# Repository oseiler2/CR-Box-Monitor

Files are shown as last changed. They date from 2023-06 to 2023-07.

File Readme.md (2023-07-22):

# Fan controller and CO2 Monitor for Corsi-Rosenthal boxes

An ESP32 based controller with integrated CO2 Monitor for PC-fans used in [Corsi-Rosenthal boxes](https://en.wikipedia.org/wiki/Corsi%E2%80%93Rosenthal_Box) and other diy air filters.

See [here](https://github.com/oseiler2/CO2Monitor) for some additional background on CO2 monitoring.

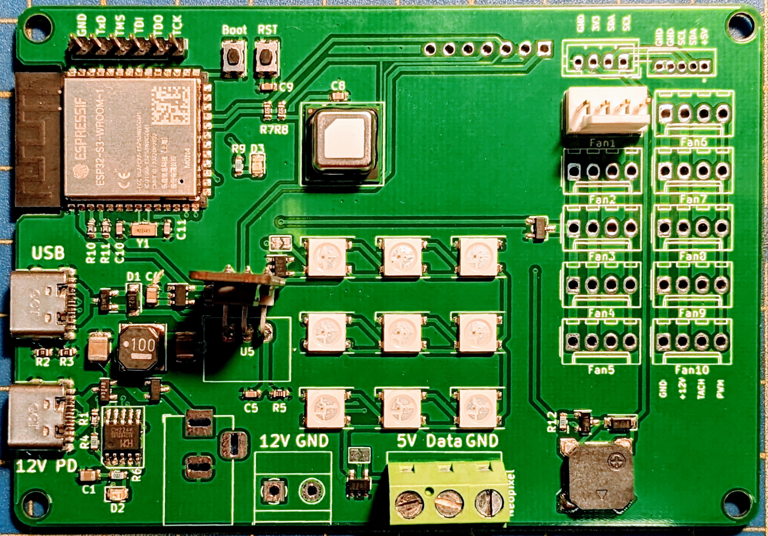
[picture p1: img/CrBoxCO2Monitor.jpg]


## Motivation

Many commercial air filters are expensive, under-dimensioned and noisy. Corsi-Rosenthal boxes are easy to make and very efficient air filters used to clean the air from airborne viral particles, allergens, smoke and other irritants.

The classic CR box design uses a box fan, which has some disadvantages:
- hard to get in some regions
- using mains voltage which can be a perceived or very real risk in some environments, e.g. classrooms
- can be noisy (depending on the fan)
- not easy to control

More recent designs have been replacing the box fan with an array of comparatively large, pressure optimised PC case fans, for example 9 x 140mm fans in a 3x3 grid on top of a 20 inch filter panel CR box. The smaller size of the fans also allows more flexibility in designing more portable CR boxes using 2 smaller filter panels.

Low speed PC fans are also much quieter and operate on safe 12V power.

By keeping the noise as low as possible and addressing the other above concerns the acceptance and tolerance of CR Boxes is increased. Commercial air cleaners are often turned off, or set to minimum levels, which contradicts their purpose. Further this controller and the operation of the fans and effectiveness can be monitored remotely.

[Learn more about this small CR box pictured below](https://github.com/oseiler2/HalfSizeCrBox)

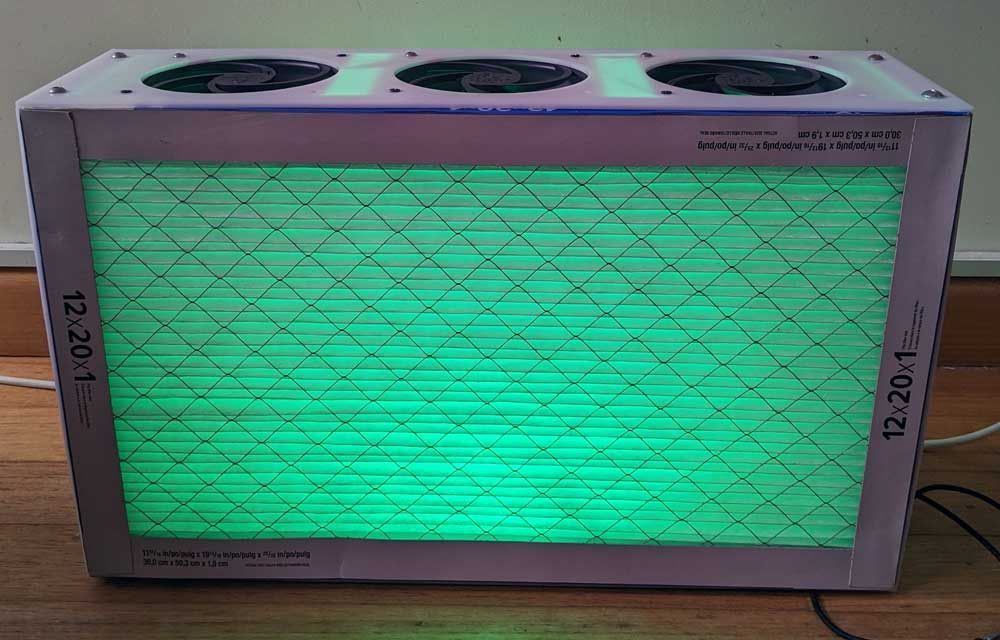
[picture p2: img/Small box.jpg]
Small CR box (https://github.com/oseiler2/HalfSizeCrBox)


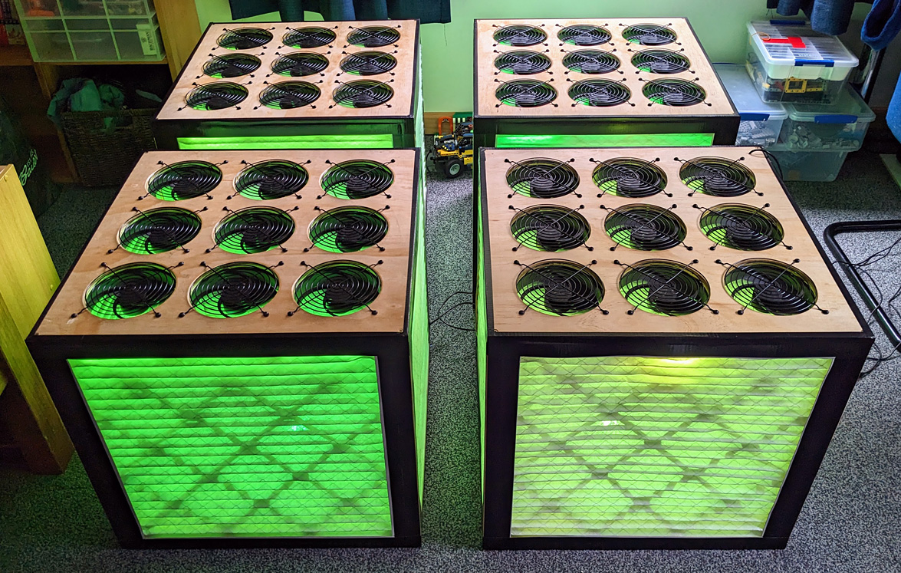
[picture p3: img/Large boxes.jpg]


# Sections

- [Features](#features) gives an overview of the capabilities and general operation
- [Hardware](#hardware) describes the board in more detail, which fans to use and how to connect them
- [PCBs](#pcbs) has more details on the design of the boards
- [Firmware](#firmware) describing the device's software features and how to use them
- [Cofiguration](#configuration) describing the device's software features and how to use them
- [Sensors](#sensors) has more information on the available sensors
- [Calibration](#calibration) has some important information on keeping the readings accurate

# Features

## General operation

The controller constantly assesses the air quality using the integrated CO2 monitor, air quality data via MQTT, or additional sensors connected via I2C, and regulates the fan speed accordingly. This will keep the airflow and related noise low while the air quality is generally good, either from good natural ventilation, or vacancy of the room. The integrated lights can reflect the air quality by showing a continuous spectrum from green via yellow to red and purple, or if configured just cycle through all colours. An integrated buzzer can also be used to alter on air quality threshold changes.

MQTT integration allows capturing all measured data and displaying on dashboards, as [documented here](https://github.com/oseiler2/CO2Monitor/blob/main/docker/docker.md).

## Key features

- Speed controller for 10 or more PC fans to regulate air flow depending on air quality
- compatible with 3 (no pwm) or 4 (pwm) pin. Non-pwm 3 pin fans are controlled using an integrated MosFET driven by a PWM signal
- 9 bright internal colour LEDs to indicate air quality with the option to connect more WS2812 (Neopixel) based LEDs
- integrated CO2, temperature and humidity sensor,
- alternatively capability to consume CO2 readings from another CO2 monitor via MQTT (eg [CO2Monitor](https://github.com/oseiler2/CO2Monitor))
- WiFi and MQTT enabled for reporting and/or consuming CO2 readings and remote configuration
- integrated buzzer to alert of poor air quality, or changes in air quality
- USB-PD compatibility to power everything off a USB-PD enabled power supply (phone charger)
- 12V direct input using 5.5x2.1mm Barrel Jack
- I2C connector to integrate other sensors
- SPS30 Particulate Matter sensor connector

# Firmware




## Firmware flashing

The firmware can be flashed onto the board directly from a supported browser [from here](https://oseiler2.github.io/CR-Box-Monitor/).

## Wifi

When not connected to a configured WiFi, the controller will automatically create an Access Point using the SSID CR-Box-<ESP32mac>. Connecting to this AP allows the Wifi credentials for the monitor to be set. The AP can also be forced by pressing the `Boot` button for less than 2 seconds.

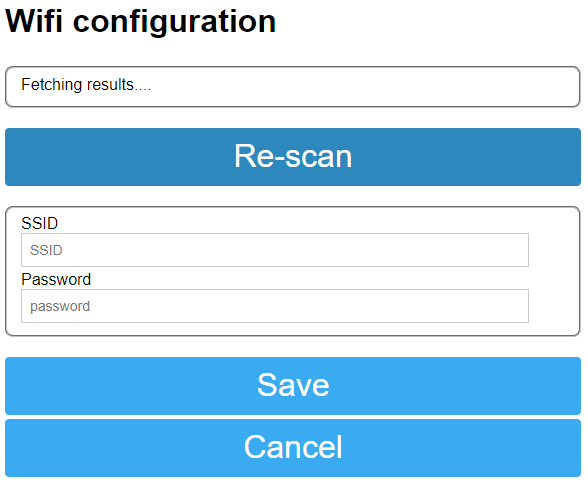
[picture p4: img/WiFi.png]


The firmware also supports WiFi configuration using [Improv Wifi](https://www.improv-wifi.com/) when connected via USB to a computer and using a supported browser [from here](https://oseiler2.github.io/CR-Box-Monitor/).

A password for the AP can be configured in the file `extra.ini` which needs to be created by copying [extra.template.ini](extra.template.ini) and applying the desired changes.

## Configuration

The controller is configured via the `config.json file on the ESP32 file system. There are 3 ways the configuration can be changed:

- via the Web Interface
- by directly editing [config.json](data/config.json) and uploading it via `Upload Filesystem Image`
- via MQTT (once connected)

### Web Interface

Navigating a browser to the controller's IP address will open the Web Interface. Here you can select to Change the Wifi configuration, the more generic device configuration, look at logs or reboot the device.

The Web Interface can be protected by setting a username and password in the file `extra.ini` which needs to be created by copying [extra.template.ini](extra.template.ini) and applying the desired changes.

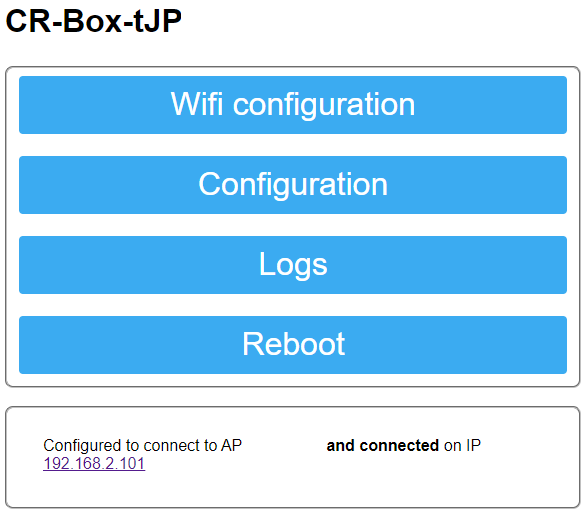
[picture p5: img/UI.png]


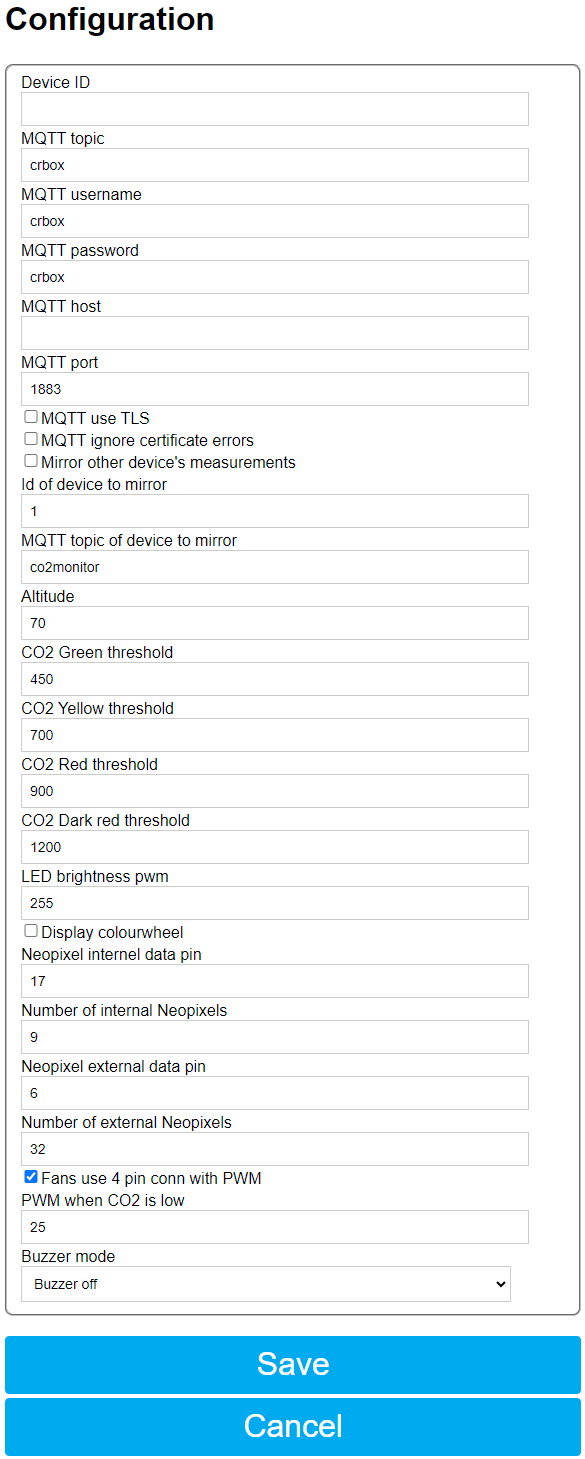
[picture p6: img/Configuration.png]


- `Device ID` unique id of the device, mainly used for MQTT
- `MQTT topic`, `MQTT username` , `MQTT password`, `MQTT host`, `MQTT port`, `MQTT TLS`, `MQTT ignore certificate errors` are all used to configure the MQTT host connection
- `Mirror other device's measurements` can be enabled to consume readings from another monitor using the `ID of device to mirror` and `MQTT topic of device to mirror` MQTT settings if the controller is not outfitted with a CO2 sensor
- `Altitude` is used to calibrate the SCD30/SCD4x CO2 sensor
- `CO2 Green threshold` sets the lower limit at which the fans will be set to idle speed. Any higher CO2 measurements increase the fan speed.
- `CO2 Yellow threshold`, `CO2 Red threshold`, `CO2 Dark threshold` set the limits for changing the LED colours and fan speed. The fan speed is continously increasing from the idle speed (green) to 50% (yellow) to full speed (red).
- `LED brightness PWM` sets the LED brightness on a scale from 0 to 255
- `Display colourwheel` changes the LEDs to circle throw all colours instead of reflecting air quality readings. This can be useful when no attention should be drawn to current CO2 levels.
- `Neopixel internal data pin` should be left at `17` and `Number of internal Neopixels` at `9` unless a different PCB configuration is being used.
- `Neopixel external data pin` should be set to `0` when no additional Neopixels are connected to the screw terminal, and set to `6` otherwise. `Number of external Neopixels` should be set to the number of additional Neopixels
- `Fans use 4 pin connector with PWM` needs to be enabled to control PWM enabled fans. If unticked the fan GND connection will be PWM driven to control 3-pin fans.
- `PWM when CO2 is low` sets the idle fan speed on a scale from 0 to 255. This should be set high enough that the fans do start up and keep spinning slowly, otherwise sufficient airflow cannot be guaranteed and the internal CO2 sensor might not give accurate readings.
- `Buzzer mode` configures the integrated buzzer to be always off, beep on every level change, or give a number of beeps depending on the CO2 level for each measurement.

### MQTT

Sensor readings can be published via MQTT for centralised storage and visualition. Each node is configured with its own id and will then publish under `crbox/<id>/up/sensors`. The top level topic `crbox` is configurable. Downlink messages to nodes can be sent to each individual node using the id in the topic `crbox/<id>/down/<command>`, or to all nodes when omitting the id part `crbox/down/<command>`

SCD3x/SCD4x

```
{
  "co2": 752,
  "temperature": "21.6",
  "humidity": "52.1",
  "fanPwm": 25
}
```

BME680

```
{
  "iaq": 19,
  "temperature": "19.2",
  "humidity": "75.6",
  "pressure": 1014
}
```

SPS30

```
{
  "pm0.5": 16,
  "pm1": 19,
  "pm2.5": 19,
  "pm4": 19,
  "pm10": 19
}
```

Sending `crbox/<id>/down/getConfig` will triger the node to reply with its current settings under `crbox/<id>/up/config`

```
{
  "appVersion": "1.0",
  "mac": "xxyyzz",
  "ip": "1.2.3.4",
  "scd40": true,
  "scd30": true,
  "bme680": true,
  "sps30": true,
  "sps30AutoCleanInt": 604800,
  "sps30Status": 0,
  "mqttTopic": "crbox",
  "mqttUsername": "crbox",
  "mqttHost": "1.2.3.4",
  "mqttServerPort": 1883,
  "mqttUseTls": true,
  "mqttInsecure": false,
  "mqttMirror": false,
  "mqttMirrordeviceId": 1,
  "mqttMirrorTopic": "co2monitor",
  "altitude": 5,
  "co2GreenThreshold": 450,
  "co2YellowThreshold": 700,
  "co2RedThreshold": 900,
  "co2DarkRedThreshold": 1200,
  "brightness": 255,
  "colourWheel": false,
  "neopixelIntData": 17,
  "neopixelIntNumber": 9,
  "neopixelExtData": 6,
  "neopixelExtNumber": 32,
  "fanHasPwm": true,
  "minPwm": 25,
  "buzzerMode": 0,
  "tempOffset": "4.0"
}
```

A message to `crbox/<id>/down/setConfig` will set the node's configuration to the provided parameters. Note that changes to the hardware configuration will trigger a reboot.

```
{
  "deviceId": 1,
  "mqttUsername": "crbox",
  "mqttPassword": "crbox",
  "mqttTopic": "crbox",
  "mqttUsername": "crbox",
  "mqttHost": "1.2.3.4",
  "mqttServerPort": 1883,
  "mqttUseTls": true,
  "mqttInsecure": false,
  "mqttMirror": false,
  "mqttMirrordeviceId": 1,
  "mqttMirrorTopic": "co2monitor",
  "altitude": 5,
  "co2GreenThreshold": 450,
  "co2YellowThreshold": 700,
  "co2RedThreshold": 900,
  "co2DarkRedThreshold": 1200,
  "brightness": 255,
  "colourWheel": false,
  "neopixelIntData": 17,
  "neopixelIntNumber": 9,
  "neopixelExtData": 6,
  "neopixelExtNumber": 32,
  "fanHasPwm": true,
  "minPwm": 25,
  "buzzerMode": 0,
  "tempOffset": "4.0"
}
```

A message to `crbox/<id>/down/setTemperatureOffset` will set the SCD3x/SCD4x's temperature offset (float, °C):

```
4.0
```

A message to `crbox/<id>/down/calibrate` will manually calibrate the SCD3x/SCD4x sensor to the given value:

```
412
```

A message to `crbox/<id>/down/setSPS30AutoCleanInterval` will set the SPS30 fan auto-clean interval in seconds to the given value:

```
604800
```

A message to `crbox/<id>/down/cleanSPS30` will run a fan clean on the SPS30.

A message to `crbox/<id>/down/installMqttRootCa` will attempt to install the pem-based ca cert in the payload as root cert for tls enabled MQTT connections. A connection attempt will be made using the configured MQTT settings and the new cert, and if successful the cert will be persisted, otherwise discarded.

A message to `crbox/<id>/down/installRootCa` will install the pem-based ca cert in the payload as root cert for OTA update requests.

A message to `crbox/<id>/down/ota` will trigger the OTA polling mechnism if configured.

A message to `crbox/<id>/down/forceota` will force an OTA update using the URL provided in the payload.

A message to `crbox/<id>/down/reboot` will trigger a reset on the node.

A message to `crbox/<id>/down/resetWifi` will wipe configured WiFi settings (SSID/password) and force a reboot.

### MQTT TLS support

To connect to an MQTT server using TLS (recommended) you need to enable TLS in the configuration by setting `mqttUseTls` to `true`. You also need to supply a root CA certificate in PEM format on the file system as `/mqtt_root_ca.pem` and/or a client certificate and key for using mTLS as `mqtt_client_cert.pem` and `mqtt_client_key.pem`. These files can be uploaded using the `Upload Filesystem Image` project task in PlatformIO. Alternatively you can set `mqttInsecure` to `true` to disable certificate validation altogether.

# Hardware

## Power

The board can be powered in 3 different ways:

1. Using a USB-PD capable power supply or phone charger, capable of delivering 12V and enough power (25W+). [charger - amazon.au](https://www.amazon.com.au/dp/B09NDG1MPP)
2. 12V direct input using 5.5x2.1mm Barrel Jack receptable
3. 12V screw terminal

Make sure to use a power supply that can deliver enough power. 140mm fans need about 150mA each. Each Neopixel can draw up to 60mA (540mA for all 9 integrated ones). The 5V DC-DC regulator is dimensioned for up to 2A - take that in mind when connecting additional Neopixels.

## Fans

Make sure to use pressure optimised low speed fans that are capable of delivering airflow at sufficient static pressure e.g. [Arctic P14](https://www.arctic.de/en/P14/ACFAN00136A) (2.4 mm H2O, 0.3 Sone, 123 m³/h) or [Arctic P12](https://www.arctic.de/en/P12/ACFAN00135A) (2.2 mm H20, 0.3 Sone, 95.7 m³/h).

The controller can read the RPM signal from the fan connected to the `Fan 1` connector

## Fan hub

The main board features up to 10 connectors for 3 or 4 pin fans. For builds where the fan cables are too short to reach to the main PCB, or when more than 10 fans should be connected, the fan hub PCB can be used to connect another 9 fans via an extension cable. To enale reading the RPM sigal connect the fan hub extension cable to the `Fan 1` connector on the main board and to the `Up` connector on the fan hub.

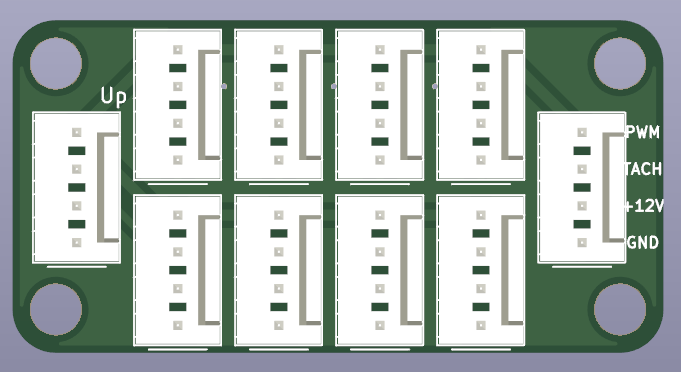
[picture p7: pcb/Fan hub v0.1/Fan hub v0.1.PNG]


## Additional Neopixels

Additional [Neopixel strips](https://www.adafruit.com/category/183) can be connected using the dedicated screw terminal. Make sure to not overload the power supply and integrated 5V 2A linear regulator.

# PCBs

Main board [sources](pcb/CrBoxCo2Monitor%20V0.1/), [gerber files](pcb/CrBoxCo2Monitor%20V0.1/CrBoxCo2Monitor%20V0.1.zip) and [parts list](pcb/CrBoxCo2Monitor%20V0.1/bom.md).

Fan hub [sources](pcb/Fan%20hub%20v0.1/) and [gerber files](pcb/Fan%20hub%20v0.1/Fan%20hub%20v0.1.zip).

3d printable [board holder](stl/PCB%20holder.STL) using M3 threaded inserts

# Sensors

The presence of supported I2C based sensors/displays will be automatically detected on start-up.

## SCD3x

A SCD3x NDIR CO2 sensor can be connected to the designated footprint and will provide CO2, temperature and humidity readings via I2C. It supports a separate ready signal which is connected to the ESP32.

## SCD4x

A SCD4x NDIR CO2 sensor can be soldered directly onto the pcb and provides CO2, temperature and humidity readings via I2C.

## BME680

A BME680 sensor can be connected via the I2C JST header [Adafruit BME680](https://www.adafruit.com/product/3660), [STEMMA to JST SH Cable](https://www.adafruit.com/product/4424) to provide additional VOC and AIQ measurements.

## SPS30 Particulate matter sensor

The SPS30 sensor can be connected to the dedicated connector using a JST-ZR cable.

## other

Other I2C based sensors can be wired using the JST-PH I2C header.

# Calibration

CO2 sensors need to be regularly calibrated to provide reliable measurements. The used sensors support auto-calibration and that is enabled in the firmware. It works by looking over measurements over a period and calibrating the lowest value against 420ppm (configurable in the firmware). This is based on the assumption that the monitor 'sees' clean outside air about once a week. If that cannot be achieved the firmware also allows for a forced calibration against a given value. Please also make sure to set the altitude setting according to the monitor location. For details please check the sensor's datasheets.

Manual calibration can be triggered by pressing the `Boot` button for more than 5 seconds. Make sure the monitor has been exposed to fresh outside air for a while and be careful not to breathe towards the monitor when doing this.

Calibration can also be triggered remotely via [MQTT](#mqtt).

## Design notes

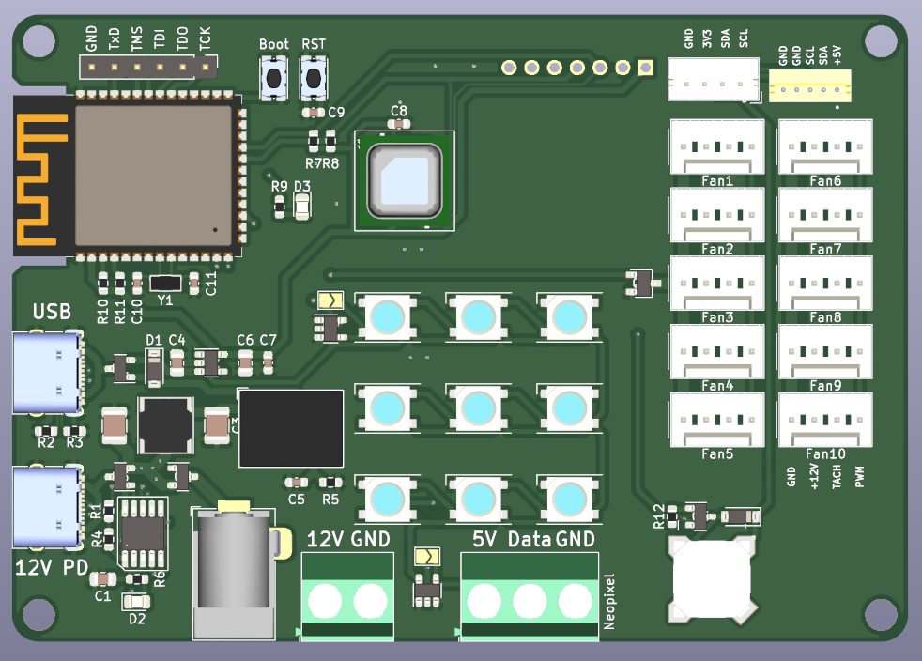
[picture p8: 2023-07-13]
pcb/CrBoxCo2Monitor V0.1/CR CO2 Monitor v0.1.png

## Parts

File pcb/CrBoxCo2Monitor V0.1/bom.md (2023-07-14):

# BOM

Note: the components marked in the 'Function' column are optional and only needed for the mentioned function.
For example if you want the second USB port to power the PCB with 12V via a USB-C PD power supply you need to populate all components marked with USB-PD.

| Quantity | Designator | Description | Function (optional) | Footprint | Part # | Supplier | Alternative |
| --- | --- | --- | --- | --- | --- | --- | --- |
| 1 | BZ1 | Buzzer | Buzzer | | ST-03BHT | [DigiKey](https://www.digikey.com/en/products/detail/soberton-inc/ST-03BHT/16354830) | |
| 1 | C1 | 10μF | USB-PD | 0805 | | | |
| 2 | C4, C6 | 10μF | | 0805 | | | |
| 1 | C2 | 10μF/50V MLCC | | 1210 | CL32B106KBJNNNE | [DigiKey](https://www.digikey.co.nz/en/products/detail/samsung-electro-mechanics/CL32B106KBJNNNE/3889045) | |
| 1 | C3 | 4.7μF/50V MLCC | | 1210 | CL32B475KBUYNNE | [DigiKey](https://www.digikey.co.nz/en/products/detail/samsung-electro-mechanics/CL32B475KBUYNNE/3886950) | |
| 4 | C5, C7, C8, C9 | 100nF | | 0603 | | | |
| 1 | D1 | Schottky diode 20V 500MA | | SOD-123 | MBR0520 | [DigiKey](https://www.digikey.co.nz/en/products/detail/micro-commercial-co/MBR0520-TP/717250) | |
| 1 | D2 | LED yellow 2mA 2.1V | USB-PD | 0805 | KPT-2012YC | [Element14](https://nz.element14.com/kingbright/kpt-2012yc/led-0805-yellow-8mcd-588nm/dp/2099243) | |
| 1 | D3 | LED green 2mA 2.65V | | 0805 | KPT-2012LVZGCK | [Element14](https://nz.element14.com/kingbright/kpt-2012lvzgck/led-green-50mcd-525nm-smd/dp/2610419) | |
| 1 | D4 | 200mA general purpose diode | Buzzer | SOD-123 | MMSD4148 | [DigiKey](https://www.digikey.co.nz/en/products/detail/onsemi/MMSD4148/1048639) | |
| 9 | D10, D11, D12, D13, D14, D15, D16, D17, D18 | WS2812B | | 5050 | | [AliExpress](https://www.aliexpress.com/item/1005002653014067.html) | |
| 1-10 | Fan1, Fan2, Fan3, Fan4, Fan5, Fan6, Fan7, Fan8, Fan9, Fan10 | 3/4 pin Molex_KK-254 | | | | [AliExpress](https://www.aliexpress.com/item/32961935772.html) | [DigiKey](https://www.digikey.com/en/products/detail/sullins-connector-solutions/SWR25X-NRTC-S04-ST-BA/2769654) |
| 1 | J1 | USB4105-GF-A-120 | | | | [DigiKey](https://www.digikey.com/en/products/detail/gct/USB4105-GF-A-120/14559037) | |
| 1 | J2 | USB4105-GF-A-120 | USB-PD | | | [DigiKey](https://www.digikey.com/en/products/detail/gct/USB4105-GF-A-120/14559037) | |
| 1 | J3 | Barrel Jack 5.5x2.1mm | 12V in DC-Barrel | | | [DigiKey](https://www.digikey.com/en/products/detail/tensility-international-corp/54-00166/10459294) | |
| 1 | J4 | Screw_Terminal_01x02 5.08 | | | | [DigiKey](https://www.digikey.com/en/products/detail/te-connectivity-amp-connectors/1776493-2/2293915) | |
| 1 | J5 | Screw_Terminal_01x03 5.08 | | | | [DigiKey](https://www.digikey.com/en/products/detail/te-connectivity-amp-connectors/282837-3/2187974) | |
| 1 | J6 | JST_PH_B4B-PH-K | optional I2C | | | [DigiKey](https://www.digikey.com/en/products/detail/jst-sales-america-inc/B4B-PH-K-S-LF-SN/926613) | |
| 1 | J7 | JST_B5B-ZR | optional SPS30 PM | | | [DigiKey](https://www.digikey.com/en/products/detail/jst-sales-america-inc/B5B-ZR-LF-SN/926567) | |
| 1 | J10 | PinHeader_1x06_P2.54mm | optional debug | | | | |
| 1 | L1 | 10μH 2.4A 59.8mOhm | | 6x6 | NRS6045T100MMGK | [DigiKey](https://www.digikey.com/en/products/detail/taiyo-yuden/NRS6045T100MMGK/2665984) | |
| 1 | Q1 | MOSFET P-CH 20V 3A | | SOT-23 | DMG2301L | [DigiKey](https://www.digikey.com/en/products/detail/diodes-incorporated/DMG2301L-7/5768820) | |
| 1 | Q2 | MOSFET P-CH 30V 3.1A | | SOT-23 | SI2343DS-T1-GE3 | [DigiKey](https://www.digikey.com/en/products/detail/vishay-siliconix/SI2343DS-T1-GE3/2622046) | |
| 1 | Q3 | MOSFET P-CH 30V 3.1A | USB-PD | SOT-23 | SI2343DS-T1-GE3 | [DigiKey](https://www.digikey.com/en/products/detail/vishay-siliconix/SI2343DS-T1-GE3/2622046) | |
| 1 | Q4 | MOSFET N-CH 20V 6.5A | | SOT-23 | DMN2053U-7 | [DigiKey](https://www.digikey.co.nz/en/products/detail/diodes-incorporated/DMN2053U-7/9769936) | |
| 1 | Q5 | BC847 | Buzzer | SOT-23 | | | |
| 1 | R1 | 10k | USB-PD | 0603 | | | |
| 2 | R11, R10 | 10k | | 0603 | | | |
| 1 | R12 | 470R | Buzzer | 0603 | | | |
| 2 | R2, R3 | 5k1 | | 0603 | | | |
| 1 | R5 | 100k | | 0603 | | | |
| 2 | R4, R6 | 1k | USB-PD | 0603 | | | |
| 1 | R9 | 1k | | 0603 | | | |
| 2 | R8, R7 | 4k7 | | 0603 | | | |
| 2 | SW2, SW1 | Tactile Switch SPST-NO | | | KMR621NG LFS | [DigiKey](https://www.digikey.co.nz/en/products/detail/c-k/KMR621NG-LFS/6035350) | |
| 1 | U1 | ESP32-S3 | | | ESP32-S3-WROOM-1-N4 | [DigiKey](https://www.digikey.com/en/products/detail/espressif-systems/ESP32-S3-WROOM-1-N4/16162639) | |
| 1 | U2 | IC REG LINEAR 3.3V 600MA | | SOT-23-5  | AP7366-33W5-7 | [DigiKey](https://www.digikey.com/en/products/detail/diodes-incorporated/AP7366-33W5-7/9867322) | |
| 1 | U3 | SCD40-D-R1 | | | | [DigiKey](https://www.digikey.co.nz/en/products/detail/sensirion-ag/SCD40-D-R2/13684003) | [DigiKey](https://www.digikey.com/en/products/detail/sensirion-ag/SCD41-D-R2/13684005) |
| 1 | U4 | SCD30 | alternative to U3 | | | [DigiKey](https://www.digikey.com/en/products/detail/sensirion-ag/SCD30/8445334) | [AliExpress](https://www.aliexpress.com/item/1005002467019989.html) |
| 1 | U5 | DC DC Converter 5V 2A | | | R-78B5.0-2.0 | [DigiKey](https://www.digikey.com/en/products/detail/recom-power/R-78B5-0-2-0/6677084) | |
| 1 | U6 | CH224K | USB-PD | ESSOP-10  | | [AliExpress](https://www.aliexpress.com/item/1005005284290184.html) | |
| 2 | U7,U8 | 74AHCT1G125 | | SOT-23-5  | | [DigiKey](https://www.digikey.com/en/products/detail/texas-instruments/SN74AHCT1G125DBVR/376028) | |

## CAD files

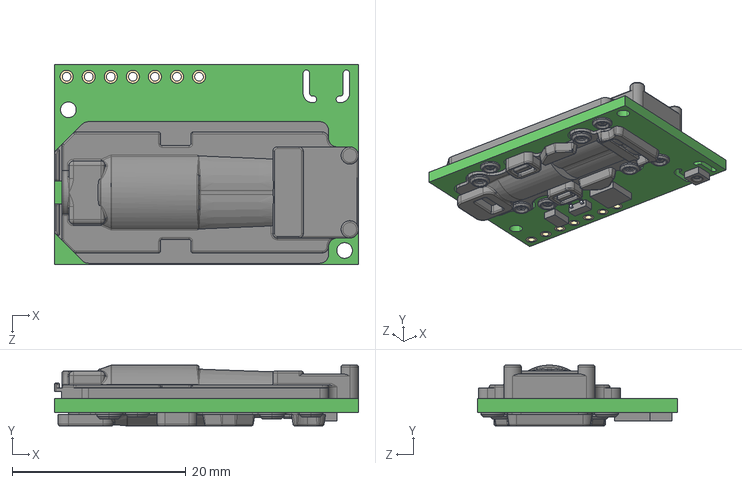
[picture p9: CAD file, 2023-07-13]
pcb/CrBoxCo2Monitor V0.1/3dmodels/SCD30--3DModel-STEP-56544.STEP
35.0 x 7.00 x 23.0 mm

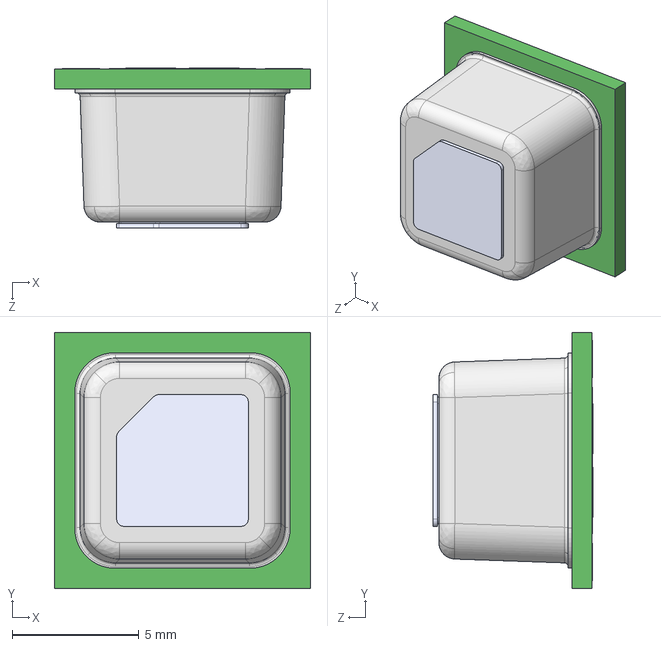
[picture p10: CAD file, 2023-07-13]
pcb/CrBoxCo2Monitor V0.1/3dmodels/SCD40-D-R2--3DModel-STEP-369182.STEP
10.1 x 10.1 x 6.31 mm

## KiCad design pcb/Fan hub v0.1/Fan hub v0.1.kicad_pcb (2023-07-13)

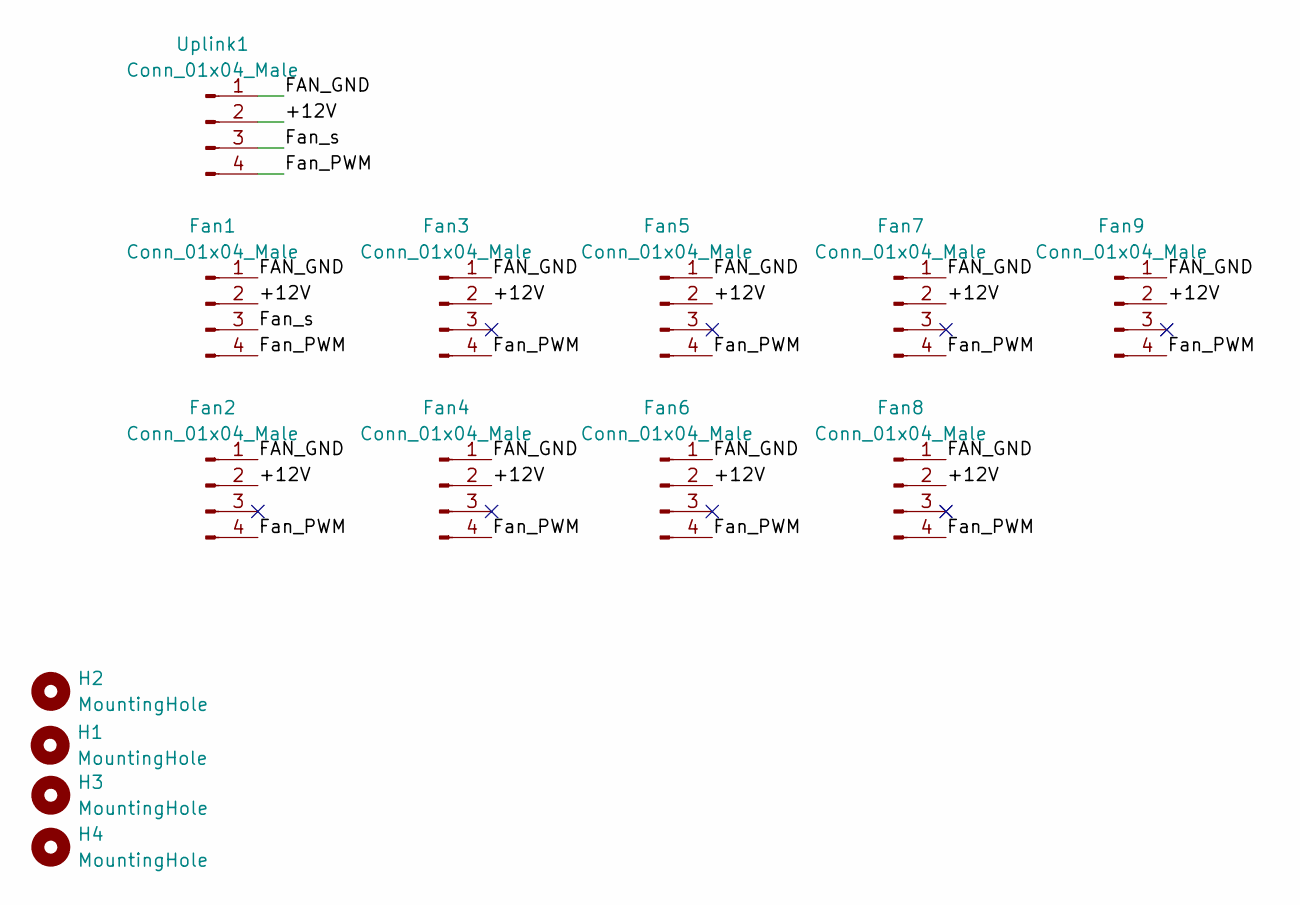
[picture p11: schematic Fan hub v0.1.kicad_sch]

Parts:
Fan1, Fan2, Fan3, Fan4, Fan5, Fan6, Fan7, Fan8, Fan9: Conn_01x04_Male; Molex_KK-254_AE-6410-04A_1x04_P2.54mm_Vertical
H1, H2, H3, H4: MountingHole; MountingHole_3.5mm
Uplink1: Conn_01x04_Male; Molex_KK-254_AE-6410-04A_1x04_P2.54mm_Vertical

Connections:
/+12V: Fan1.2, Fan2.2, Fan3.2, Fan4.2, Fan5.2, Fan6.2, Fan7.2, Fan8.2, Fan9.2, Uplink1.2
/FAN_GND: Fan1.1, Fan2.1, Fan3.1, Fan4.1, Fan5.1, Fan6.1, Fan7.1, Fan8.1, Fan9.1, Uplink1.1
/Fan_PWM: Fan1.4, Fan2.4, Fan3.4, Fan4.4, Fan5.4, Fan6.4, Fan7.4, Fan8.4, Fan9.4, Uplink1.4
/Fan_s: Fan1.3, Uplink1.3

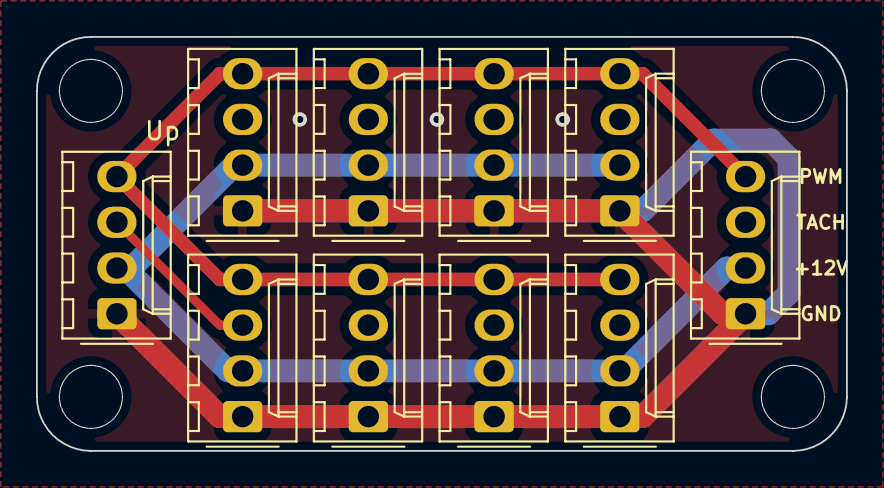
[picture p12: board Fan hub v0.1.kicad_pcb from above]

Board: 2 copper layers, 45.0 x 23.0 mm, 14 parts (0 on the bottom side), 4 nets.

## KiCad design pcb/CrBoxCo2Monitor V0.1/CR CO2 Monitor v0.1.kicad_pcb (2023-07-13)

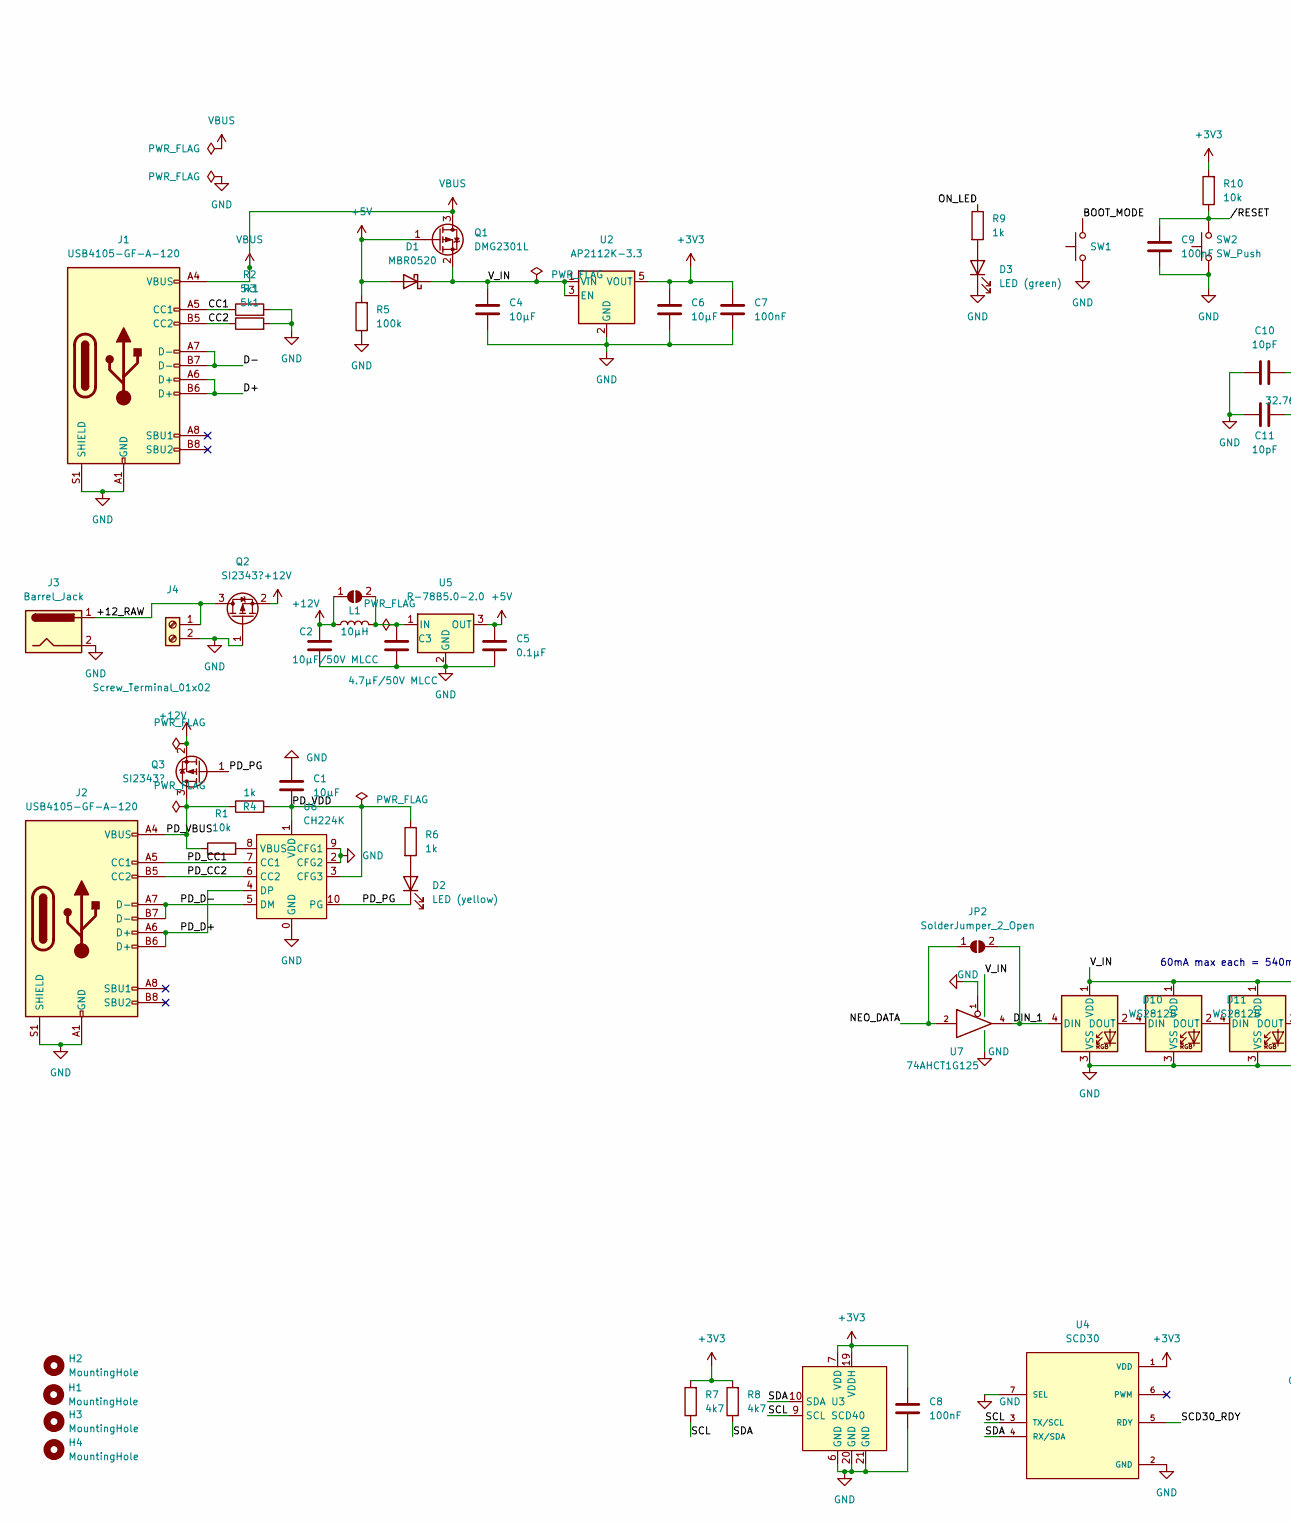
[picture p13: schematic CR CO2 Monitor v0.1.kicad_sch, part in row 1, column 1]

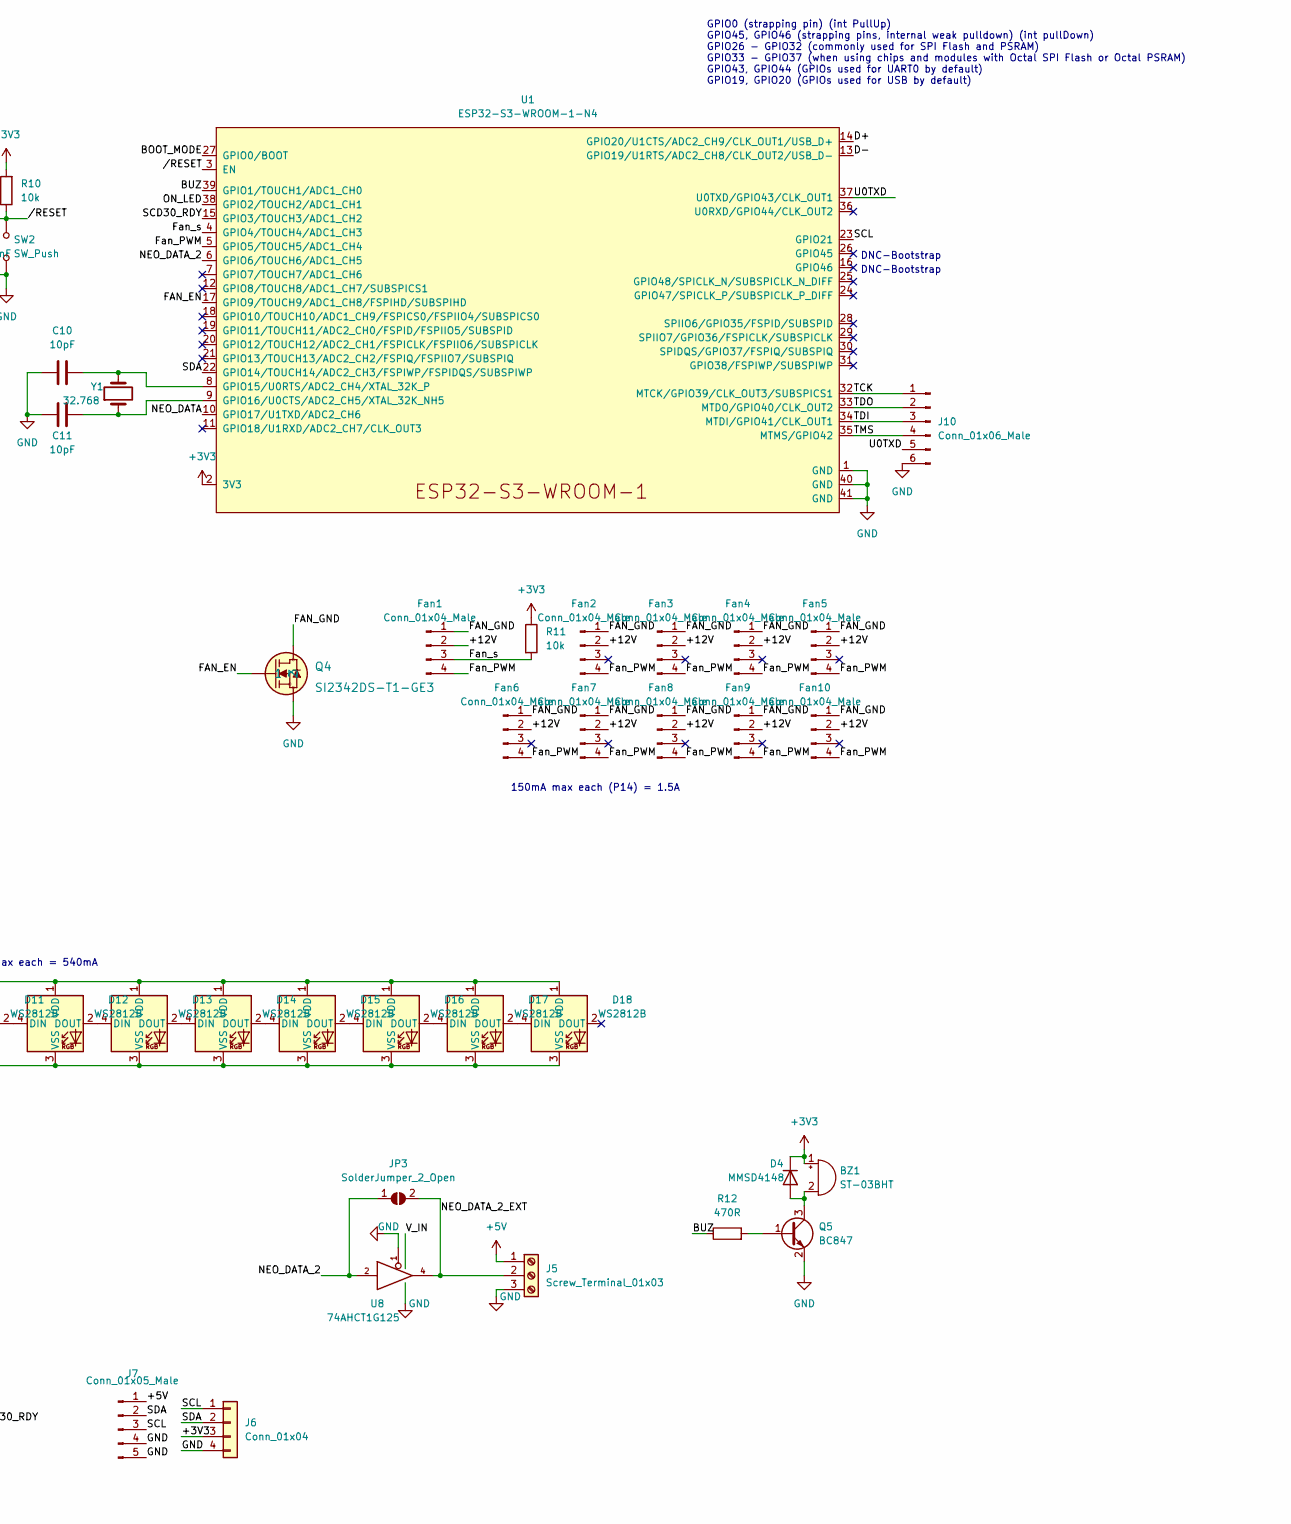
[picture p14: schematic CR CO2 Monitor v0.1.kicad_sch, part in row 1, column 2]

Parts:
BZ1: ST-03BHT; XDCR_SMT-0827-S-HT-R
C1, C4, C6: 10μF; C_0805_2012Metric
C2: 10μF/50V MLCC; C_1210_3225Metric
C3: 4.7μF/50V MLCC; C_1210_3225Metric
C5: 0.1μF; C_0603_1608Metric
C7, C8, C9: 100nF; C_0603_1608Metric
C10, C11: 10pF; C_0603_1608Metric
D1: MBR0520; D_SOD-123
D2: LED (yellow); LED_0805_2012Metric
D3: LED (green); LED_0805_2012Metric
D4: MMSD4148; D_SOD-123
D10, D11, D12, D13, D14, D15, D16, D17, D18: WS2812B; LED_WS2812B_PLCC4_5.0x5.0mm_P3.2mm
Fan1, Fan2, Fan3, Fan4, Fan5, Fan6, Fan7, Fan8, Fan9, Fan10: Conn_01x04_Male; Molex_KK-254_AE-6410-04A_1x04_P2.54mm_Vertical
H1, H2, H3, H4: MountingHole; MountingHole_3.5mm
J1, J2: USB4105-GF-A-120; USB_C_Receptacle_XKB_U262-16XN-4BVC11; JLCPCB TYPE-C-31-M-12
J3: Barrel_Jack; BarrelJack_Horizontal
J4: Screw_Terminal_01x02; TerminalBlock_Phoenix_MKDS-1,5-2-5.08_1x02_P5.08mm_Horizont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
J5: Screw_Terminal_01x03; TerminalBlock_Phoenix_MKDS-1,5-3-5.08_1x03_P5.08mm_Horizont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
J6: Conn_01x04; JST_PH_B4B-PH-K_1x04_P2.00mm_Vertical
J7: Conn_01x05_Male; JST_B5B-ZR(LF)(SN)
J10: Conn_01x06_Male; PinHeader_1x06_P2.54mm_Vertical
JP1, JP2, JP3: SolderJumper_2_Open; SolderJumper-2_P1.3mm_Open_TrianglePad1.0x1.5mm
L1: 10μH; L_Taiyo-Yuden_NR-60xx
Q1: DMG2301L; SOT-23
Q2, Q3: SI2343?; SOT-23
Q4: SI2342DS-T1-GE3; TSOT-23
Q5: BC847; SOT-23
R1, R10, R11: 10k; R_0603_1608Metric
R2, R3: 5k1; R_0603_1608Metric
R4, R6, R9: 1k; R_0603_1608Metric
R5: 100k; R_0603_1608Metric
R7, R8: 4k7; R_0603_1608Metric
R12: 470R; R_0603_1608Metric
SW1, SW2: SW_Push; SW_Push_1P1T_NO_CK_KMR2
U1: ESP32-S3-WROOM-1-N4; ESP32-S3-WROOM-1
U2: AP2112K-3.3; SOT-23-5
U3: SCD40; SCD40-D-R1
U4: SCD30; PARTREV D1
U5: R-78B5.0-2.0; Converter_DCDC_RECOM_R-78B-2.0_THT
U6: CH224K; CH224K-ESSOP-10
U7, U8: 74AHCT1G125; SOT-23-5
Y1: 32.768; Crystal_SMD_3215-2Pin_3.2x1.5mm; Digikey CM7VT1A32.768KHZ125PF20PPMTBQAT3

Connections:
+3V3: BZ1.1 (-), C6.1, C7.1, C8.1, D4.1 (K), J6.3, R7.2, R8.2, R10.2, R11.1, U1.2 (3V3), U2.5 (VOUT), U3.7 (VDD), U3.19 (VDDH), U4.1 (VDD)
+5V: C5.1, D1.2 (A), J5.1, J7.1, Q1.1 (G), R5.2, U5.3 (OUT)
+12V: C2.1, Fan1.2, Fan2.2, Fan3.2, Fan4.2, Fan5.2, Fan6.2, Fan7.2, Fan8.2, Fan9.2, Fan10.2, JP1.1 (A), L1.1, Q2.2 (S), Q3.2 (S)
/+12_RAW: J3.1, J4.1, Q2.3 (D)
/BOOT_MODE: SW1.2, U1.27 (GPIO0/BOOT)
/BUZ: R12.1, U1.39 (GPIO1/TOUCH1/ADC1_CH0)
/CC1: J1.A5 (CC1), R2.1
/CC2: J1.B5 (CC2), R3.1
/D+: J1.A6 (D+), J1.B6 (D+), U1.14 (GPIO20/U1CTS/ADC2_CH9/CLK_OUT1/USB_D+)
/D-: J1.A7 (D-), J1.B7 (D-), U1.13 (GPIO19/U1RTS/ADC2_CH8/CLK_OUT2/USB_D-)
/DIN_1: D10.4 (DIN), JP2.2 (B), U7.4
/FAN_EN: Q4.1, U1.17 (GPIO9/TOUCH9/ADC1_CH8/FSPIHD/SUBSPIHD)
/FAN_GND: Fan1.1, Fan2.1, Fan3.1, Fan4.1, Fan5.1, Fan6.1, Fan7.1, Fan8.1, Fan9.1, Fan10.1, Q4.3
/Fan_PWM: Fan1.4, Fan2.4, Fan3.4, Fan4.4, Fan5.4, Fan6.4, Fan7.4, Fan8.4, Fan9.4, Fan10.4, U1.5 (GPIO5/TOUCH5/ADC1_CH4)
/Fan_s: Fan1.3, R11.2, U1.4 (GPIO4/TOUCH4/ADC1_CH3)
/NEO_DATA: JP2.1 (A), U1.10 (GPIO17/U1TXD/ADC2_CH6), U7.2
/NEO_DATA_2: JP3.1 (A), U1.6 (GPIO6/TOUCH6/ADC1_CH5), U8.2
/NEO_DATA_2_EXT: J5.2, JP3.2 (B), U8.4
/ON_LED: R9.1, U1.38 (GPIO2/TOUCH2/ADC1_CH1)
/PD_CC1: J2.A5 (CC1), U6.7 (CC1)
/PD_CC2: J2.B5 (CC2), U6.6 (CC2)
/PD_D+: J2.A6 (D+), J2.B6 (D+), U6.4 (DP)
/PD_D-: J2.A7 (D-), J2.B7 (D-), U6.5 (DM)
/PD_PG: D2.1 (K), Q3.1 (G), U6.10 (PG)
/PD_VBUS: J2.A4 (VBUS), J2.A9 (VBUS), J2.B4 (VBUS), J2.B9 (VBUS), Q3.3 (D), R1.1, R4.1
/PD_VDD: C1.2, R4.2, R6.1, U6.1 (VDD), U6.3 (CFG3)
/SCD30_RDY: U1.15 (GPIO3/TOUCH3/ADC1_CH2), U4.5 (RDY)
/SCL: J6.1, J7.3, R7.1, U1.23 (GPIO21), U3.9 (SCL), U4.3 (TX/SCL)
/SDA: J6.2, J7.2, R8.1, U1.22 (GPIO14/TOUCH14/ADC2_CH3/FSPIWP/FSPIDQS/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), U3.10 (SDA), U4.4 (RX/SDA)
/TCK: J10.1, U1.32 (MTCK/GPIO39/CLK_OUT3/SUBSPICS1)
/TDI: J10.3, U1.34 (MTDI/GPIO41/CLK_OUT1)
/TDO: J10.2, U1.33 (MTDO/GPIO40/CLK_OUT2)
/TMS: J10.4, U1.35 (MTMS/GPIO42)
/U0TXD: J10.5, U1.37 (U0TXD/GPIO43/CLK_OUT1)
//RESET: C9.1, R10.1, SW2.2, U1.3 (EN)
GND: C1.1, C2.2, C3.2, C4.2, C5.2, C6.2, C7.2, C8.2, C9.2, C10.1, C11.1, D3.1 (K), D10.3 (VSS), D11.3 (VSS), D12.3 (VSS), D13.3 (VSS), D14.3 (VSS), D15.3 (VSS), D16.3 (VSS), D17.3 (VSS), D18.3 (VSS), J1.A1 (GND), J1.A12 (GND), J1.B1 (GND), J1.B12 (GND), J1.S1 (SHIELD), J2.A1 (GND), J2.A12 (GND), J2.B1 (GND), J2.B12 (GND), J2.S1 (SHIELD), J3.2, J4.2, J5.3, J6.4, J7.4, J7.5, J10.6, Q2.1 (G), Q4.2, Q5.2 (E), R2.2, R3.2, R5.1, SW1.1, SW2.1, U1.1 (GND), U1.40 (GND), U1.41 (GND), U2.2 (GND), U3.6 (GND), U3.20 (GND), U3.21 (GND), U4.2 (GND), U4.7 (SEL), U5.2 (GND), U6.0 (GND), U6.2 (CFG2), U6.9 (CFG1), U7.1, U7.3 (GND), U8.1, U8.3 (GND)
unnamed: BZ1.2 (+), D4.2 (A), Q5.3 (C)
unnamed: C3.1, JP1.2 (B), L1.2, U5.1 (IN)
unnamed: C10.2, U1.8 (GPIO15/U0RTS/ADC2_CH4/XTAL_32K_P), Y1.2
unnamed: C11.2, U1.9 (GPIO16/U0CTS/ADC2_CH5/XTAL_32K_NH5), Y1.1
unnamed: D2.2 (A), R6.2
unnamed: D3.2 (A), R9.2
unnamed: D10.2 (DOUT), D11.4 (DIN)
unnamed: D11.2 (DOUT), D12.4 (DIN)
unnamed: D12.2 (DOUT), D13.4 (DIN)
unnamed: D13.2 (DOUT), D14.4 (DIN)
unnamed: D14.2 (DOUT), D15.4 (DIN)
unnamed: D15.2 (DOUT), D16.4 (DIN)
unnamed: D16.2 (DOUT), D17.4 (DIN)
unnamed: D17.2 (DOUT), D18.4 (DIN)
unnamed: Q5.1 (B), R12.2
unnamed: R1.2, U6.8 (VBUS)
VBUS: J1.A4 (VBUS), J1.A9 (VBUS), J1.B4 (VBUS), J1.B9 (VBUS), Q1.3 (D)
VCC: C4.1, D1.1 (K), D10.1 (VDD), D11.1 (VDD), D12.1 (VDD), D13.1 (VDD), D14.1 (VDD), D15.1 (VDD), D16.1 (VDD), D17.1 (VDD), D18.1 (VDD), Q1.2 (S), U2.1 (VIN), U2.3 (EN), U7.5 (VCC), U8.5 (VCC)

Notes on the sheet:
DNC-Bootstrap
60mA max each = 540mA
GPIO0 (strapping pin) (int PullUp) GPIO45, GPIO46 (strapping pins, internal weak pulldown) (int pullDown) GPIO26 - GPIO32 (commonly used for SPI Flash and PSRAM) GPIO33 - GPIO37 (when using chips and modules with Octal SPI Flash or Octal PSRAM) GPIO43, GPIO44 (GPIOs used for UART0 by default) GPIO1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
150mA max each (P14) = 1.5A

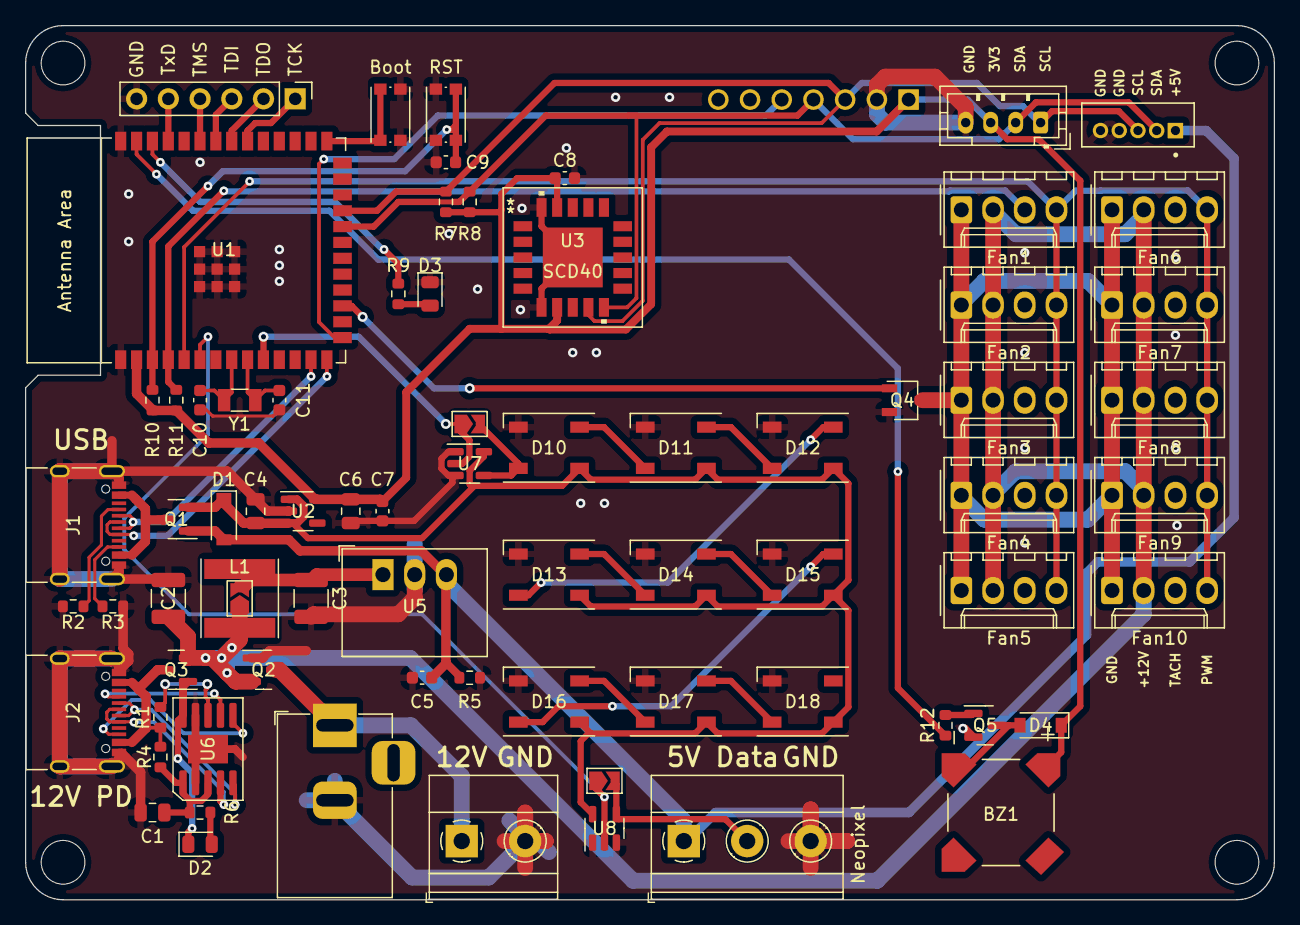
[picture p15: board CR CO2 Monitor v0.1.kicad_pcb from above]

Board: 2 copper layers, 100.0 x 70.0 mm, 79 parts (1 on the bottom side), 54 nets.

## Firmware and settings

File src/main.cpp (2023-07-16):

#include <logging.h>
#include <globals.h>
#include <Arduino.h>
#include <config.h>

#include <WiFi.h>
#include <Wire.h>
#include <i2c.h>
#include <esp_event.h>
#include <esp_err.h>
#include <esp_task_wdt.h>
#include <rom/rtc.h>

#include <configManager.h>
#include <mqtt.h>
#include <sensors.h>
#include <scd30.h>
#include <scd40.h>
#include <sps_30.h>
#include <housekeeping.h>
#include <neopixel.h>
#include <buzzer.h>
#include <wifiManager.h>
#include <ota.h>
#include <model.h>
#include <fan.h>

// Local logging tag
static const char TAG[] = __FILE__;

Model* model;
Neopixel* neopixel;
Buzzer* buzzer;
SCD30* scd30;
SCD40* scd40;
SPS_30* sps30;
Fan* fan;
TaskHandle_t sensorsTask;
TaskHandle_t wifiManagerTask;

bool hasLEDs = false;
bool hasNeoPixel = false;
bool hasBuzzer = false;
bool hasBattery = false;


const uint32_t debounceDelay = 50;
volatile uint32_t lastBtn1DebounceTime = 0;
volatile uint8_t button1State = 0;
uint8_t oldConfirmedButton1State = 0;
uint32_t lastConfirmedBtn1PressedTime = 0;

void ICACHE_RAM_ATTR button1Handler() {
  button1State = (digitalRead(BTN_1) ? 0 : 1);
  lastBtn1DebounceTime = millis();
}

void prepareOta() {}

void updateMessage(char const* msg) {}

void setPriorityMessage(char const* msg) {}

void clearPriorityMessage() {}

void modelUpdatedEvt(uint16_t mask, TrafficLightStatus oldStatus, TrafficLightStatus newStatus) {
  if (hasNeoPixel && neopixel) neopixel->update(mask, oldStatus, newStatus);
  if (hasBuzzer && buzzer) buzzer->update(mask, oldStatus, newStatus);
  if (fan) fan->update(mask, oldStatus, newStatus);
  if ((mask & M_PRESSURE) && I2C::scd40Present() && scd40) scd40->setAmbientPressure(model->getPressure());
  if ((mask & M_PRESSURE) && I2C::scd30Present() && scd30) scd30->setAmbientPressure(model->getPressure());
  if ((mask & ~M_CONFIG_CHANGED) != M_NONE) {
    char buf[8];
    DynamicJsonDocument* doc = new DynamicJsonDocument(512);
    if (mask & M_CO2) (*doc)["co2"] = model->getCo2();
    if (mask & M_TEMPERATURE) {
      sprintf(buf, "%.1f", model->getTemperature());
      (*doc)["temperature"] = buf;
    }
    if (mask & M_HUMIDITY) {
      sprintf(buf, "%.1f", model->getHumidity());
      (*doc)["humidity"] = buf;
    }
    if (mask & M_PRESSURE) (*doc)["pressure"] = model->getPressure();
    if (mask & M_IAQ) (*doc)["iaq"] = model->getIAQ();
    if (mask & M_PM0_5) (*doc)["pm0.5"] = model->getPM0_5();
    if (mask & M_PM1_0) (*doc)["pm1"] = model->getPM1();
    if (mask & M_PM2_5) (*doc)["pm2.5"] = model->getPM2_5();
    if (mask & M_PM4) (*doc)["pm4"] = model->getPM4();
    if (mask & M_PM10) (*doc)["pm10"] = model->getPM10();
    (*doc)["fanPwm"] = fan->getFanPwm();
    mqtt::publishSensors(doc);
  }
}

void configChanged() {
  model->configurationChanged();
}

void calibrateCo2SensorCallback(uint16_t co2Reference) {
  ESP_LOGI(TAG, "Starting calibration");
  if (I2C::scd30Present() && scd30) scd30->calibrateScd30ToReference(co2Reference);
  if (I2C::scd40Present() && scd40) scd40->calibrateScd40ToReference(co2Reference);
  vTaskDelay(pdMS_TO_TICKS(200));
}

void setTemperatureOffsetCallback(float temperatureOffset) {
  if (I2C::scd30Present() && scd30) scd30->setTemperatureOffset(temperatureOffset);
  if (I2C::scd40Present() && scd40) scd40->setTemperatureOffset(temperatureOffset);
}

float getTemperatureOffsetCallback() {
  if (I2C::scd30Present() && scd30) return scd30->getTemperatureOffset();
  if (I2C::scd40Present() && scd40) return scd40->getTemperatureOffset();
  return NaN;
}

uint32_t getSPS30AutoCleanInterval() {
  if (I2C::sps30Present && sps30) return sps30->getAutoCleanInterval();
  return 0;
}

boolean setSPS30AutoCleanInterval(uint32_t intervalInSeconds) {
  if (I2C::sps30Present && sps30) return sps30->setAutoCleanInterval(intervalInSeconds);
  return false;
}

boolean cleanSPS30() {
  if (I2C::sps30Present && sps30) return sps30->clean();
  return false;
}

uint8_t getSPS30Status() {
  if (I2C::sps30Present && sps30) return sps30->getStatus();
  return false;
}

void logCoreInfo() {
  esp_chip_info_t chip_info;
  esp_chip_info(&chip_info);
  ESP_LOGI(TAG,
    "This is ESP32 chip with %d CPU cores, WiFi%s%s, silicon revision "
    "%d, %dMB %s Flash",
    chip_info.cores,
    (chip_info.features & CHIP_FEATURE_BT) ? "/BT" : "",
    (chip_info.features & CHIP_FEATURE_BLE) ? "/BLE" : "",
    chip_info.revision, spi_flash_get_chip_size() / (1024 * 1024),
    (chip_info.features & CHIP_FEATURE_EMB_FLASH) ? "embedded"
    : "external");
  ESP_LOGI(TAG, "Internal Total heap %d, internal Free Heap %d",
    ESP.getHeapSize(), ESP.getFreeHeap());
#ifdef BOARD_HAS_PSRAM
  ESP_LOGI(TAG, "SPIRam Total heap %d, SPIRam Free Heap %d",
    ESP.getPsramSize(), ESP.getFreePsram());
#endif
  ESP_LOGI(TAG, "ChipRevision %d, Cpu Freq %d, SDK Version %s",
    ESP.getChipRevision(), ESP.getCpuFreqMHz(), ESP.getSdkVersion());
  ESP_LOGI(TAG, "Flash Size %d, Flash Speed %d", ESP.getFlashChipSize(),
    ESP.getFlashChipSpeed());
}

void setup() {
  esp_task_wdt_init(20, true);

  if (LED_PIN >= 0) {
    pinMode(LED_PIN, OUTPUT);
    digitalWrite(LED_PIN, LOW);
  }
  pinMode(BTN_1, INPUT_PULLUP);
  Serial.begin(115200);
  esp_log_set_vprintf(logging::logger);
  esp_log_level_set("*", ESP_LOG_VERBOSE);
  ESP_LOGI(TAG, "CO2 Monitor v%s. Built from %s @ %s", APP_VERSION, SRC_REVISION, BUILD_TIMESTAMP);

  model = new Model(modelUpdatedEvt);

  logCoreInfo();

  RESET_REASON resetReason = rtc_get_reset_reason(0);

  ESP_ERROR_CHECK(esp_event_loop_create_default());
  ESP_ERROR_CHECK(esp_event_handler_instance_register(WIFI_EVENT, ESP_EVENT_ANY_ID, WifiManager::eventHandler, NULL, NULL));
  ESP_ERROR_CHECK(esp_event_handler_instance_register(IP_EVENT, IP_EVENT_STA_GOT_IP, WifiManager::eventHandler, NULL, NULL));

  setupConfigManager();
  if (!loadConfiguration(config)) {
    getDefaultConfiguration(config);
    saveConfiguration(config);
  }
  logConfiguration(config);

  WifiManager::setupWifiManager("CR-Box", getConfigParameters(), false, true,
    updateMessage, setPriorityMessage, clearPriorityMessage, configChanged);

  hasNeoPixel = (config.neopixelIntData != 0 && config.neopixelIntNumber != 0);
  hasBuzzer = config.buzzerPin != 0;

  if (hasNeoPixel) {
    pinMode(config.neopixelIntData, OUTPUT);
    digitalWrite(config.neopixelIntData, LOW);
  }
  if (hasBuzzer) {
    pinMode(config.buzzerPin, OUTPUT);
    digitalWrite(config.buzzerPin, LOW);
  }

  Wire.begin((int)SDA_PIN, (int)SCL_PIN, (uint32_t)I2C_CLK);

  I2C::initI2C();

  if (I2C::scd30Present()) scd30 = new SCD30(&Wire, model, updateMessage);
  if (I2C::scd40Present()) scd40 = new SCD40(&Wire, model, updateMessage);
  if (I2C::sps30Present()) sps30 = new SPS_30(&Wire, model, updateMessage);

  if (hasNeoPixel) neopixel = new Neopixel(model, config.neopixelIntData, config.neopixelIntNumber);
  if (hasBuzzer) buzzer = new Buzzer(model, config.buzzerPin);
  fan = new Fan(model);

  mqtt::setupMqtt(
    "CrBox",
    model,
    calibrateCo2SensorCallback,
    setTemperatureOffsetCallback,
    getTemperatureOffsetCallback,
    getSPS30AutoCleanInterval,
    setSPS30AutoCleanInterval,
    cleanSPS30,
    getSPS30Status,
    configChanged);

  char msg[128];
  sprintf(msg, "Reset reason: %u", resetReason);
  mqtt::publishStatusMsg(msg);

  xTaskCreatePinnedToCore(mqtt::mqttLoop,  // task function
    "mqttLoop",         // name of task
    8192,               // stack size of task
    (void*)1,           // parameter of the task
    2,                  // priority of the task
    &mqtt::mqttTask,    // task handle
    0);                 // CPU core

  xTaskCreatePinnedToCore(OTA::otaLoop,  // task function
    "otaLoop",          // name of task
    8192,               // stack size of task
    (void*)1,           // parameter of the task
    2,                  // priority of the task
    &OTA::otaTask,      // task handle
    1);                 // CPU core

  if (scd30 || scd40 || sps30) {
    Sensors::setupSensorsLoop(scd30, scd40, sps30);
    sensorsTask = Sensors::start(
      "sensorsLoop",      // name of task
      4096,               // stack size of task
      2,                  // priority of the task
      1);                 // CPU core
  }

  wifiManagerTask = WifiManager::start(
    "wifiManagerLoop",  // name of task
    8192,               // stack size of task
    2,                  // priority of the task
    1);                 // CPU core

  housekeeping::cyclicTimer.attach(30, housekeeping::doHousekeeping);

  OTA::setupOta(prepareOta, setPriorityMessage, clearPriorityMessage);

  attachInterrupt(BTN_1, button1Handler, CHANGE);

  ESP_LOGI(TAG, "Setup done.");
}

void loop() {
  if (button1State != oldConfirmedButton1State && (millis() - lastBtn1DebounceTime) > debounceDelay) {
    oldConfirmedButton1State = button1State;
    if (oldConfirmedButton1State == 1) {
      lastConfirmedBtn1PressedTime = millis();
    } else if (oldConfirmedButton1State == 0) {
      uint32_t btnPressTime = millis() - lastConfirmedBtn1PressedTime;
      ESP_LOGD(TAG, "lastConfirmedBtnPressedTime - millis() %u", btnPressTime);
      if (btnPressTime < 2000) {
        if (LED_PIN >= 0) digitalWrite(LED_PIN, LOW);
        prepareOta();
        WifiManager::startCaptivePortal();
      } else if (btnPressTime > 5000) {
        calibrateCo2SensorCallback(420);
      }
    }
  }
  vTaskDelay(pdMS_TO_TICKS(50));
}

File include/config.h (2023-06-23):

#ifndef _CONFIG_H
#define _CONFIG_H

#include <logging.h>
#include <sdkconfig.h>

#define OTA_URL               "https://otahost/crbox/firmware.json"
#define OTA_APP               "crbox"
//#define OTA_POLL


#if CONFIG_IDF_TARGET_ESP32

#define LED_PIN                2
#define BUZZER_PIN             4
#define BTN_1                  0
#define NEO_DATA_INT          16
#define NEO_DATA_EXT          17
#define FAN_HALL              25
#define FAN_PWM               26
#define FAN_EN                27
#define SDA_PIN              SDA
#define SCL_PIN              SCL
#define SCD30_RDY_PIN         35

#elif CONFIG_IDF_TARGET_ESP32S3

#define LED_PIN                2
#define BUZZER_PIN             1
#define BTN_1                  0
#define NEO_DATA_INT          17
#define NEO_DATA_EXT           6
#define XTAL_32k_1            15
#define XTAL_32k_2            16
#define FAN_HALL               4
#define FAN_PWM                5
#define FAN_EN                 9
#define SDA_PIN               14
#define SCL_PIN               21
#define SCD30_RDY_PIN          3

#endif

#define I2C_CLK 100000UL
#define SCD30_I2C_CLK 50000UL   // SCD30 recommendation of 50kHz

static const char* CONFIG_FILENAME = "/config.json";
static const char* MQTT_ROOT_CA_FILENAME = "/mqtt_root_ca.pem";
static const char* MQTT_CLIENT_CERT_FILENAME = "/mqtt_client_cert.pem";
static const char* MQTT_CLIENT_KEY_FILENAME = "/mqtt_client_key.pem";
static const char* TEMP_MQTT_ROOT_CA_FILENAME = "/temp_mqtt_root_ca.pem";
static const char* ROOT_CA_FILENAME = "/root_ca.pem";

#define MQTT_QUEUE_LENGTH      25

#define PWM_CHANNEL_FAN         0
#define PWM_CHANNEL_BUZZER      2

// ----------------------------  Config struct ------------------------------------- 
#define CONFIG_SIZE 1280

#define MQTT_USERNAME_LEN 20
#define MQTT_PASSWORD_LEN 20
#define MQTT_HOSTNAME_LEN 30
#define MQTT_TOPIC_LEN 30
#define SSID_LEN 32
#define WIFI_PASSWORD_LEN 64

typedef enum : uint8_t {
  BUZ_OFF = 0,
  BUZ_LVL_CHANGE,
  BUZ_ALWAYS
} BuzzerMode;

struct Config {
  uint16_t deviceId;
  char mqttTopic[MQTT_TOPIC_LEN + 1];
  char mqttUsername[MQTT_USERNAME_LEN + 1];
  char mqttPassword[MQTT_PASSWORD_LEN + 1];
  char mqttHost[MQTT_HOSTNAME_LEN + 1];
  bool mqttUseTls;
  bool mqttInsecure;
  bool mqttMirrorDevice;
  uint16_t mqttMirrordeviceId;
  char mqttMirrorTopic[MQTT_TOPIC_LEN + 1];
  uint16_t mqttServerPort;
  uint16_t altitude;
  uint16_t co2GreenThreshold;
  uint16_t co2YellowThreshold;
  uint16_t co2RedThreshold;
  uint16_t co2DarkRedThreshold;
  uint8_t brightness;
  bool colourWheel;
  uint8_t neopixelIntData;
  uint8_t neopixelIntNumber;
  uint8_t neopixelExtData;
  uint8_t neopixelExtNumber;
  uint8_t minPwm;
  uint8_t buzzerPin = BUZZER_PIN;
  bool fanHasPwm;
  BuzzerMode buzzerMode = BUZ_LVL_CHANGE;
};

#endif

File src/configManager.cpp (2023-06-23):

#include <configManager.h>

#include <FS.h>
#include <LittleFS.h>
#include <ArduinoJson.h>

// Local logging tag
static const char TAG[] = __FILE__;

Config config;

// Allocate a temporary JsonDocument
// Don't forget to change the capacity to match your requirements.
// Use arduinojson.org/v6/assistant to compute the capacity.
/*
{
  "deviceId": 65535,
  "mqttTopic": "123456789112345678921",
  "mqttUsername": "123456789112345678921",
  "mqttPassword": "123456789112345678921",
  "mqttHost": "1234567891123456789212345678931",
  "mqttUseTls": false,
  "mqttInsecure": false,
  "mqttServerPort": 65535,
  "mqttMirrorDevice" false,
  "mqttMirrordeviceId": 65535,
  "mqttMirrorTopic": "123456789112345678921",
  "altitude": 12345,
  "co2GreenThreshold": 0,
  "co2YellowThreshold": 800,
  "co2RedThreshold": 1000,
  "co2DarkRedThreshold": 2000,
  "brightness": 255,
  "buzzerMode": 0,
  "ssd1306Rows": 64,
  "neopixelIntData": 17,
  "neopixelIntNumber": 6,
  "neopixelExtData": 32,
  "neopixelIExNumber": 9,
  "sleepModeOledLed": 0,
  "fanHasPwm": false,
  "minPwm": 30
}
*/

#define DEFAULT_DEVICE_ID                          0
#define DEFAULT_MQTT_TOPIC                   "crbox"
#define DEFAULT_MQTT_HOST                "127.0.0.1"
#define DEFAULT_MQTT_PORT                       1883
#define DEFAULT_MQTT_USERNAME                "crbox"
#define DEFAULT_MQTT_PASSWORD                "crbox"
#define DEFAULT_MQTT_USE_TLS                   false
#define DEFAULT_MQTT_INSECURE                  false
#define DEFAULT_MQTT_MIRROR                    false
#define DEFAULT_MQTT_MIRROR_DEVICE_ID              0
#define DEFAULT_MQTT_MIRROR_TOPIC       "co2monitor"
#define DEFAULT_ALTITUDE                           5
#define DEFAULT_CO2_GREEN_THRESHOLD              420
#define DEFAULT_CO2_YELLOW_THRESHOLD             700
#define DEFAULT_CO2_RED_THRESHOLD                900
#define DEFAULT_CO2_DARK_RED_THRESHOLD          1200
#define DEFAULT_BRIGHTNESS                       255
#define DEFAULT_COLOURWHEEL                    false
#define DEFAULT_NEOPIXEL_INT_DATA       NEO_DATA_INT
#define DEFAULT_NEOPIXEL_INT_NUMBER                9
#define DEFAULT_NEOPIXEL_EXT_DATA       NEO_DATA_EXT
#define DEFAULT_NEOPIXEL_EXT_NUMBER               32
#define DEFAULT_FAN_HAS_PWM                    false
#define DEFAULT_MIN_PWM                           30
#define DEFAULT_BUZZER_MODE                  BUZ_OFF

std::vector<ConfigParameterBase<Config>*> configParameterVector;

const char* BUZZER_MODE_STRINGS[] = {
  "Buzzer off",
  "Buzzer when level changes",
  "Buzzer always on",
};
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

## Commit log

2023-07-13 PCBs and BOM
    [CR CO2 Monitor v0.1.kicad_pcb, CR CO2 Monitor v0.1.kicad_sch, Fan hub v0.1.kicad_pcb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]
2023-07-14 Correct footprint
2023-07-16 Add fan pwm to MQTT data
2023-07-18 Change fan PWM frequency to 40kHz
